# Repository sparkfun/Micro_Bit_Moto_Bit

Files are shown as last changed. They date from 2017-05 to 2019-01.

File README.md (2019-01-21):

SparkFun moto:bit
========================================

SparkFun moto:bit

[*SparkFun moto:bit (DEV-14213)*](https://www.sparkfun.com/products/14213)

The SparkFun moto:bit is a fully loaded “carrier” board for the micro:bit that, when combined with the micro:bit, provides you with a fully functional robotics platform. The moto:bit offers a simple, beginner-friendly robotics controller capable of operating a basic robotics chassis. Onboard each moto:bit are multiple I/O pins capable of hooking up servos, sensors and other circuits. At the flip of the switch you can get your micro:bit moving!

Repository Contents
-------------------

* **/Firmware** - Example code used in the micro:bot Kit Experiment Guide and Wireless Remote Control with micro:bit tutorials. While they are compiled HEX codes, you can modify the example code once they are imported into MakeCode editor.
* **/Hardware** - Eagle design files (.brd, .sch)
* **/Production** - Production panel files (.brd)

Documentation
--------------
* **[Library](https://github.com/sparkfun/pxt-moto-bit)** - PXT gamer:bit firmware
* **[micro:bot Kit Experiment Guide](https://learn.sparkfun.com/tutorials/microbot-kit-experiment-guide/)** - Experiment guide using the moto:bit carrier board.
* **[Wireless Remote Control with micro:bit](https://learn.sparkfun.com/tutorials/wireless-remote-control-with-microbit)** - Project guide using the micro:bot and micro:arcade kits. By utilizing the radio blocks, you can wirelessly control the micro:bot using the gamer:bit.

License Information
-------------------

This product is _**open source**_! 

Please review the LICENSE.md file for license information. 

If you have any questions or concerns on licensing, please contact techsupport@sparkfun.com.

Distributed as-is; no warranty is given.

- Your friends at SparkFun.

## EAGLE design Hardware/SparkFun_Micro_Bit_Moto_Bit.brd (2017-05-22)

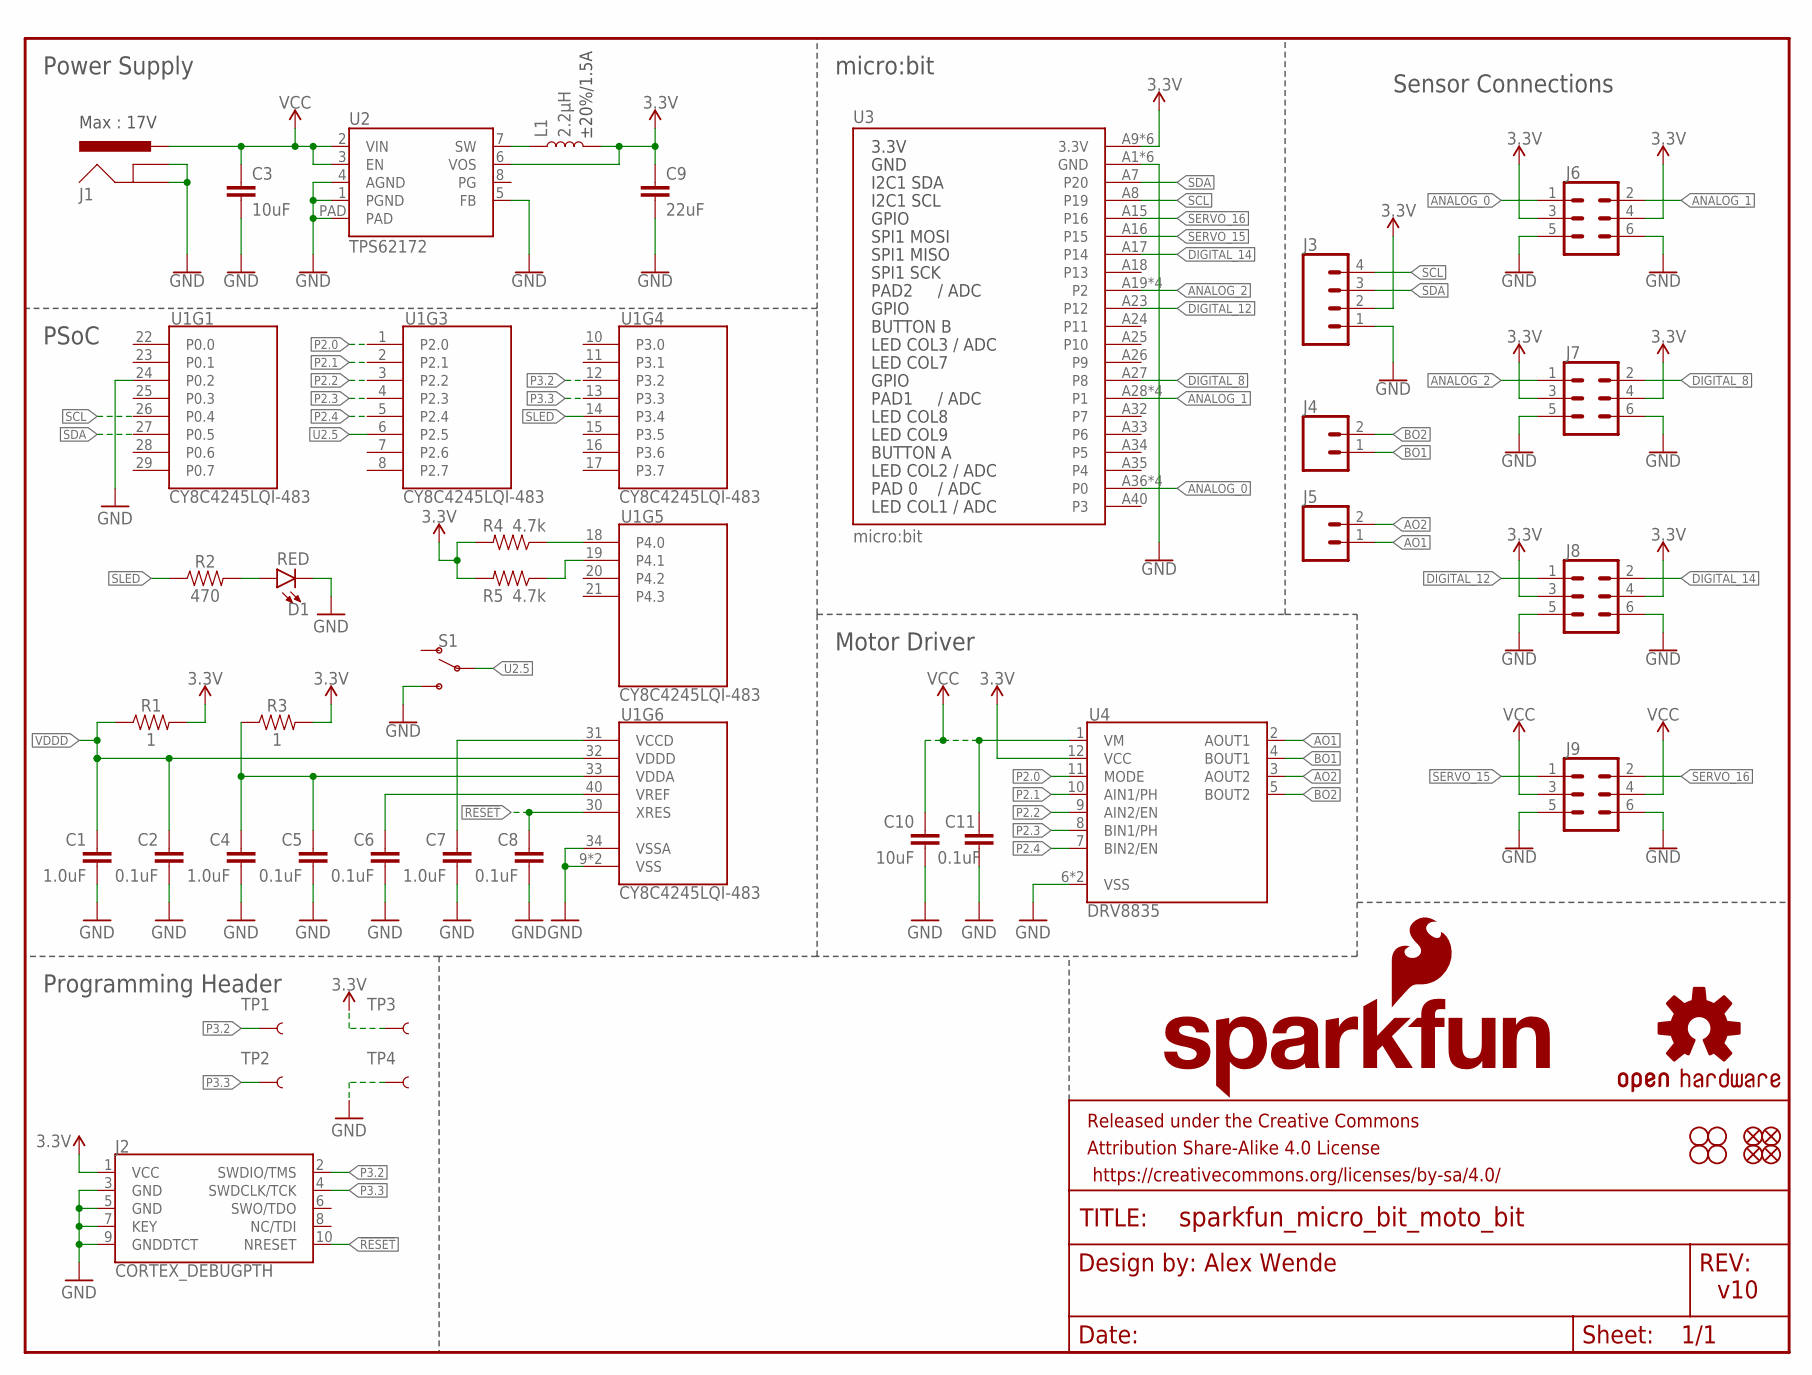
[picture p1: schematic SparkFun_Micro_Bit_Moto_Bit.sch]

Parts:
C1, C4, C7: 1.0uF; 0603
C2, C5, C6, C8, C11: 0.1uF; 0603
C3, C10: 10uF; 1210
C9: 22uF; 0805
D1: RED; LED-0603
FD1, FD2, FD3, FD4: FIDUCIALUFIDUCIAL; FIDUCIAL-MICRO
FRAME1: FRAME-LETTER; CREATIVE_COMMONS
H1, H2, H3, H4: STAND-OFF
J1: POWER_JACKPTH_LOCK; POWER_JACK_PTH_LOCK
J2: CORTEX_DEBUGPTH; 2X5-PTH-1.27MM
J3: CONN_04SMD_STRAIGHT_COMBO; 1X04_SMD_VERTICAL_COMBO
J4, J5: CONN_02PTH_RA_FEMALE; 1X02_RA_FEMALE
J6, J7, J8, J9: CONN_03X2SMT; 2X3_SMT_POSTS
L1: 2.2µH; INDUCTOR_2.2UH
LOGO1: SFE_LOGO_NAME_FLAME.3_INCH; SFE_LOGO_NAME_FLAME_.3
LOGO2: OSHW-LOGOL; OSHW-LOGO-L
R1, R3: 1; 0603
R2: 470; 0603
R4, R5: 4.7k; 0603
S1: SWITCH-SPDT-PTH-11.6X4.0MM; SWITCH_SPDT_PTH_11.6X4.0MM
TP1, TP2, TP3, TP4: TEST-POINT3; PAD.03X.03
U1: CY8C4245LQI-483; QFN-40
U2: TPS62172; WSON-8-PAD
U3: micro:bit; MICRO:BIT_RA_PTH
U4: DRV8835; WSON-12

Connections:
3.3V: C9.1, J2.1 (VCC), J3.2, J6.3, J6.4, J7.3, J7.4, J8.3, J8.4, L1.P$2 (2), R1.2, R3.2, R4.2, R5.2, TP3.P$1, U2.6 (VOS), U3.A9 (3.3V), U3.A10 (3.3V), U3.A11 (3.3V), U3.A12 (3.3V), U3.A13 (3.3V), U3.A14 (3.3V), U4.12 (VCC)
!RESET: C8.1, J2.10 (NRESET), U1.30 (XRES)
ANALOG_0: J6.1, U3.A36 (P0), U3.A37 (P0), U3.A38 (P0), U3.A39 (P0)
ANALOG_1: J6.2, U3.A28 (P1), U3.A29 (P1), U3.A30 (P1), U3.A31 (P1)
ANALOG_2: J7.1, U3.A19 (P2), U3.A20 (P2), U3.A21 (P2), U3.A22 (P2)
AO1: J5.1, U4.2 (AOUT1)
AO2: J5.2, U4.3 (AOUT2)
BO1: J4.1, U4.4 (BOUT1)
BO2: J4.2, U4.5 (BOUT2)
DIGITAL_8: J7.2, U3.A27 (P8)
DIGITAL_12: J8.1, U3.A23 (P12)
DIGITAL_14: J8.2, U3.A17 (P14)
GND: C1.2, C2.2, C3.2, C4.2, C5.2, C6.2, C7.2, C8.2, C9.2, C10.2, C11.2, D1.C, J1.GND, J1.GNDBREAK, J2.3 (GND), J2.5 (GND), J2.7 (KEY), J2.9 (GNDDTCT), J3.1, J6.5, J6.6, J7.5, J7.6, J8.5, J8.6, J9.5, J9.6, S1.3 (S), TP4.P$1, U1.9 (VSS), U1.24 (P0.2), U1.34 (VSSA), U1.EP (VSS), U2.1 (PGND), U2.4 (AGND), U2.5 (FB), U2.PAD, U3.A1 (GND), U3.A2 (GND), U3.A3 (GND), U3.A4 (GND), U3.A5 (GND), U3.A6 (GND), U4.6 (VSS), U4.PAD (VSS)
unnamed: C7.1, U1.31 (VCCD)
unnamed: C6.1, U1.40 (VREF)
unnamed: C4.1, C5.1, R3.1, U1.33 (VDDA)
unnamed: L1.P$1 (1), U2.7 (SW)
unnamed: R4.1, U1.18 (P4.0)
unnamed: R5.1, U1.19 (P4.1)
unnamed: D1.A, R2.2
P2.0: U1.1 (P2.0), U4.11 (MODE)
P2.1: U1.2 (P2.1), U4.10 (AIN1/PH)
P2.2: U1.3 (P2.2), U4.9 (AIN2/EN)
P2.3: U1.4 (P2.3), U4.8 (BIN1/PH)
P2.4: U1.5 (P2.4), U4.7 (BIN2/EN)
P3.2: J2.2 (SWDIO/TMS), TP1.P$1, U1.12 (P3.2)
P3.3: J2.4 (SWDCLK/TCK), TP2.P$1, U1.13 (P3.3)
SCL: J3.4, U1.26 (P0.4), U3.A8 (P19)
SDA: J3.3, U1.27 (P0.5), U3.A7 (P20)
SERVO_15: J9.1, U3.A16 (P15)
SERVO_16: J9.2, U3.A15 (P16)
SLED: R2.1, U1.14 (P3.4)
U2.5: S1.2, U1.6 (P2.5)
VCC: C3.1, C10.1, C11.1, J1.PWR, J9.3, J9.4, U2.2 (VIN), U2.3 (EN), U4.1 (VM)
VDDD: C1.1, C2.1, R1.1, U1.32 (VDDD)

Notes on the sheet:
±20%/1.5A
Power Supply
Motor Driver
Sensor Connections
micro:bit
Alex Wende
v10
PSoC
Programming Header
Max : 17V

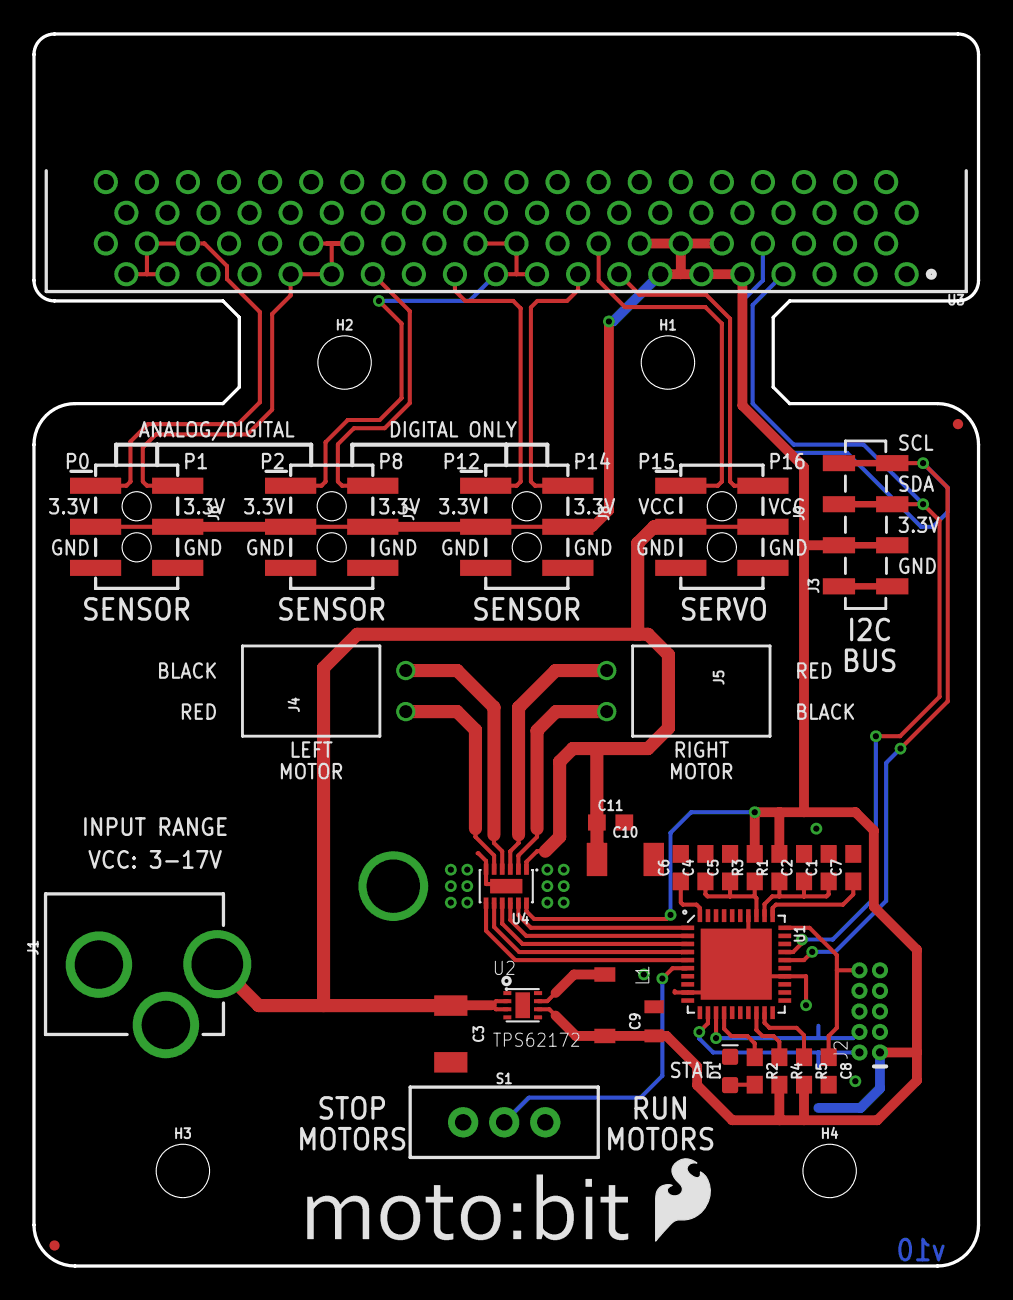
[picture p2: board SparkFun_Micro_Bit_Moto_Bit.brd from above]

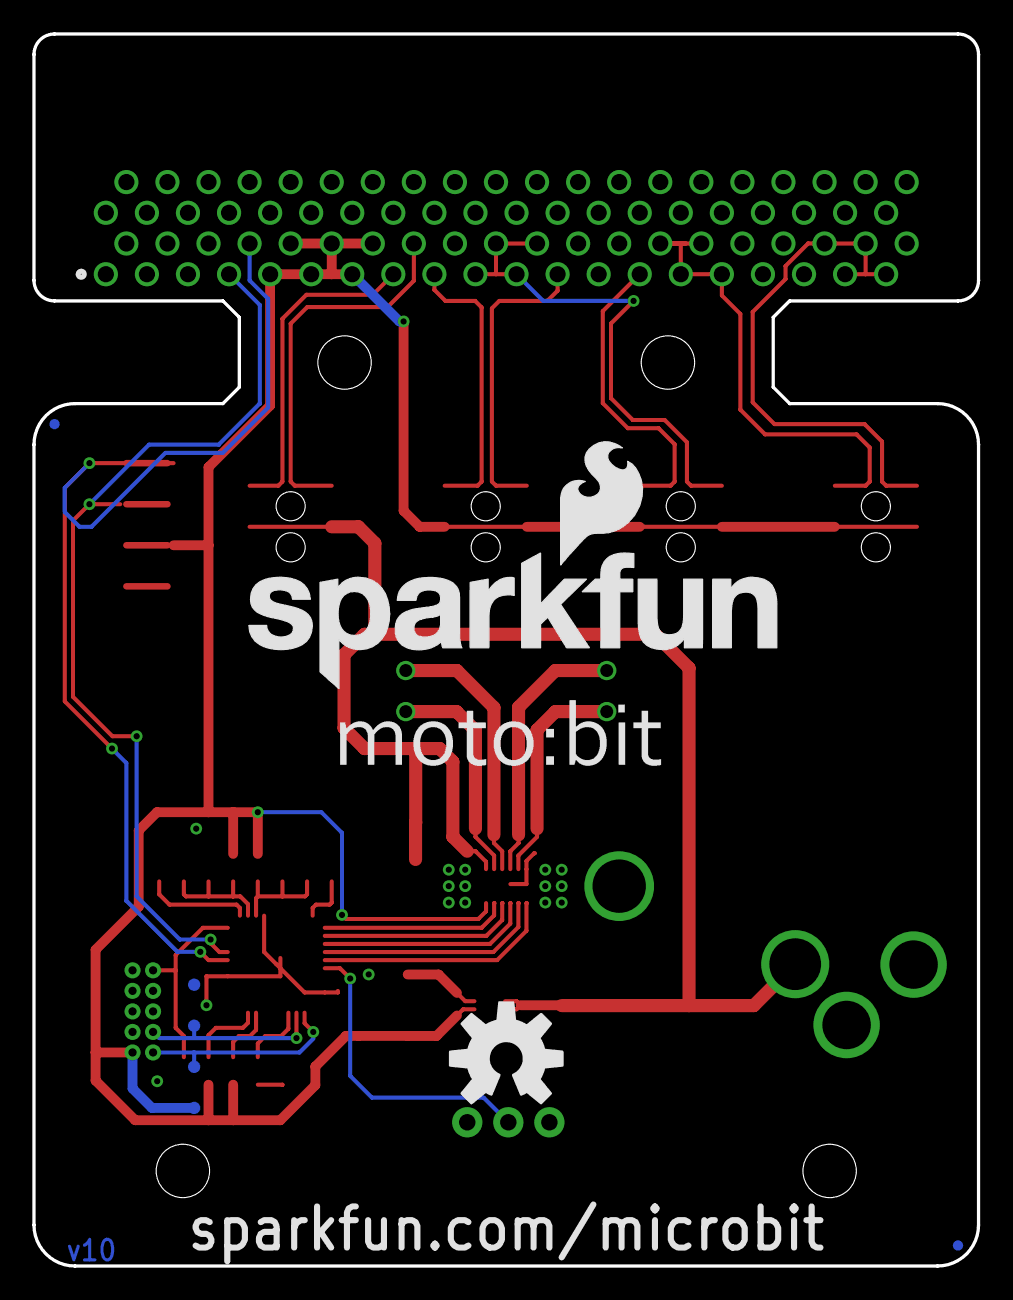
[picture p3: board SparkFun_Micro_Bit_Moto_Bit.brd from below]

Board: 2 copper layers, 58.4 x 76.2 mm, 51 parts (9 on the bottom side), 35 nets.

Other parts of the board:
U$1: PRODUCTION_INSTRUCTIONS
U$2: SFE_LOGO_FLAME_.2
U$3, U$4: LOGO-MOTOBIT

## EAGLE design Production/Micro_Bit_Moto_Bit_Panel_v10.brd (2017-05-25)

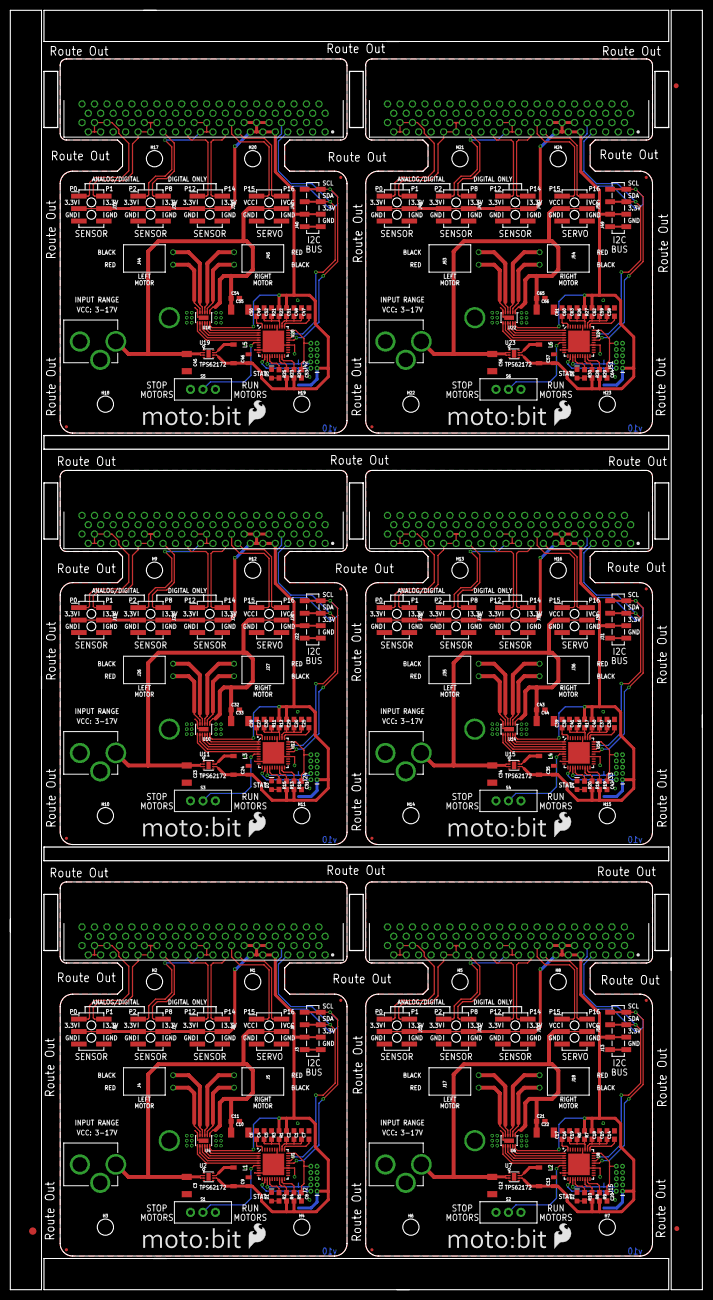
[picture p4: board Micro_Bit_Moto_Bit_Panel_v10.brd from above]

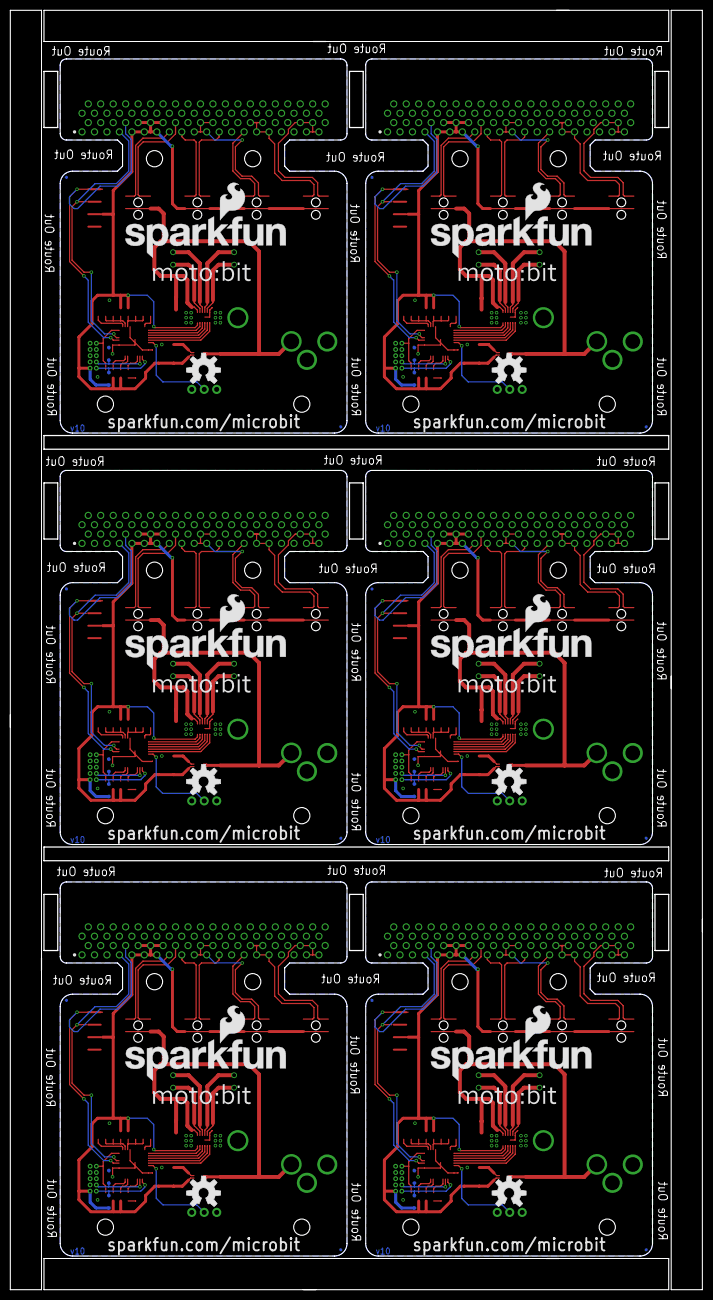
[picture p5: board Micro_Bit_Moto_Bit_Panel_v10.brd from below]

Board: 2 copper layers, 141.0 x 260.6 mm, 297 parts (54 on the bottom side), 210 nets.

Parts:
C1, C4, C7, C14, C15, C16, C25, C26, C27, C36, C37, C38, C47, C48, C49, C58, C59, C60: 1.0uF; 0603
C2, C5, C6, C8, C11, C17, C18, C19, C20, C21, C28, C29, C30, C31, C32, C39, C40, C41, C42, C43, C50, C51, C52, C53, C54, C61, C62, C63, C64, C65: 0.1uF; 0603
C3, C10, C12, C22, C23, C33, C34, C44, C45, C55, C56, C66: 10uF; 1210
C9, C13, C24, C35, C46, C57: 22uF; 0805
D1, D2, D3, D4, D5, D6: RED; LED-0603
E$1: FIDUCIAL-1.5X3
E$5, E$7: FIDUCIAL-1X2
FD1, FD2, FD3, FD4, FD5, FD6, FD7, FD8, FD9, FD10, FD11, FD12, FD13, FD14, FD15, FD16, FD17, FD18, FD19, FD20, FD21, FD22, FD23, FD24: FIDUCIALUFIDUCIAL; FIDUCIAL-MICRO
H1, H2, H3, H4, H5, H6, H7, H8, H9, H10, H11, H12, H13, H14, H15, H16, H17, H18, H19, H20, H21, H22, H23, H24: STAND-OFF
J1, J14, J23, J32, J41, J50: POWER_JACKPTH_LOCK; POWER_JACK_PTH_LOCK
J2, J15, J24, J33, J42, J51: CORTEX_DEBUGPTH; 2X5-PTH-1.27MM
J3, J13, J22, J31, J40, J49: 1X04_SMD_VERTICAL_COMBO
J4, J5, J17, J18, J26, J27, J35, J36, J44, J45, J53, J54: 1X02_RA_FEMALE
J6, J7, J8, J9, J10, J11, J12, J16, J19, J20, J21, J25, J28, J29, J30, J34, J37, J38, J39, J43, J46, J47, J48, J52: 2X3_SMT_POSTS
L1, L2, L3, L4, L5, L6: 2.2µH; INDUCTOR_2.2UH
LOGO1, LOGO3, LOGO5, LOGO7, LOGO9, LOGO11: SFE_LOGO_NAME_FLAME.3_INCH; SFE_LOGO_NAME_FLAME_.3
LOGO2, LOGO4, LOGO6, LOGO8, LOGO10, LOGO12: OSHW-LOGOL; OSHW-LOGO-L
R1, R3, R6, R7, R11, R12, R16, R17, R21, R22, R26, R27: 1; 0603
R2, R10, R15, R20, R25, R30: 470; 0603
R4, R5, R8, R9, R13, R14, R18, R19, R23, R24, R28, R29: 4.7k; 0603
S1, S2, S3, S4, S5, S6: SWITCH_SPDT_PTH_11.6X4.0MM
TP1, TP2, TP3, TP4, TP5, TP6, TP7, TP8, TP9, TP10, TP11, TP12, TP13, TP14, TP15, TP16, TP17, TP18, TP19, TP20, TP21, TP22, TP23, TP24: PAD.03X.03
U1, U8, U12, U16, U20, U24: CY8C4245LQI-483; QFN-40
U2, U7, U11, U15, U19, U23: TPS62172; WSON-8-PAD
U3, U5, U9, U13, U17, U21: micro:bit; MICRO:BIT_RA_PTH
U4, U6, U10, U14, U18, U22: DRV8835; WSON-12
U$2, U$5, U$8, U$11, U$14, U$17: SFE_LOGO_FLAME_.2
U$3, U$4, U$6, U$7, U$9, U$10, U$12, U$13, U$15, U$16, U$18, U$19: LOGO-MOTOBIT

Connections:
3.3V: C9.1, J2.1, J3.2, J6.3, J6.4, J7.3, J7.4, J8.3, J8.4, L1.P$2, R1.2, R3.2, R4.2, R5.2, TP3.P$1, U2.6, U3.A9, U3.A10, U3.A11, U3.A12, U3.A13, U3.A14, U4.12
3.3V1: C13.1, J10.3, J10.4, J11.3, J11.4, J12.3, J12.4, J13.2, J15.1, L2.P$2, R6.2, R7.2, R8.2, R9.2, TP7.P$1, U5.A9, U5.A10, U5.A11, U5.A12, U5.A13, U5.A14, U6.12, U7.6
3.3V2: C24.1, J19.3, J19.4, J20.3, J20.4, J21.3, J21.4, J22.2, J24.1, L3.P$2, R11.2, R12.2, R13.2, R14.2, TP11.P$1, U9.A9, U9.A10, U9.A11, U9.A12, U9.A13, U9.A14, U10.12, U11.6
3.3V3: C35.1, J28.3, J28.4, J29.3, J29.4, J30.3, J30.4, J31.2, J33.1, L4.P$2, R16.2, R17.2, R18.2, R19.2, TP15.P$1, U13.A9, U13.A10, U13.A11, U13.A12, U13.A13, U13.A14, U14.12, U15.6
3.3V4: C46.1, J37.3, J37.4, J38.3, J38.4, J39.3, J39.4, J40.2, J42.1, L5.P$2, R21.2, R22.2, R23.2, R24.2, TP19.P$1, U17.A9, U17.A10, U17.A11, U17.A12, U17.A13, U17.A14, U18.12, U19.6
3.3V5: C57.1, J46.3, J46.4, J47.3, J47.4, J48.3, J48.4, J49.2, J51.1, L6.P$2, R26.2, R27.2, R28.2, R29.2, TP23.P$1, U21.A9, U21.A10, U21.A11, U21.A12, U21.A13, U21.A14, U22.12, U23.6
!RESET: C8.1, J2.10, U1.30
!RESET1: C20.1, J15.10, U8.30
!RESET2: C31.1, J24.10, U12.30
!RESET3: C42.1, J33.10, U16.30
!RESET4: C53.1, J42.10, U20.30
!RESET5: C64.1, J51.10, U24.30
ANALOG_0: J6.1, U3.A36, U3.A37, U3.A38, U3.A39
ANALOG_1: J6.2, U3.A28, U3.A29, U3.A30, U3.A31
ANALOG_2: J7.1, U3.A19, U3.A20, U3.A21, U3.A22
ANALOG_3: J11.1, U5.A19, U5.A20, U5.A21, U5.A22
ANALOG_4: J10.2, U5.A28, U5.A29, U5.A30, U5.A31
ANALOG_5: J10.1, U5.A36, U5.A37, U5.A38, U5.A39
ANALOG_6: J20.1, U9.A19, U9.A20, U9.A21, U9.A22
ANALOG_7: J19.2, U9.A28, U9.A29, U9.A30, U9.A31
ANALOG_8: J19.1, U9.A36, U9.A37, U9.A38, U9.A39
ANALOG_9: J29.1, U13.A19, U13.A20, U13.A21, U13.A22
ANALOG_10: J28.2, U13.A28, U13.A29, U13.A30, U13.A31
ANALOG_11: J28.1, U13.A36, U13.A37, U13.A38, U13.A39
ANALOG_12: J38.1, U17.A19, U17.A20, U17.A21, U17.A22
ANALOG_13: J37.2, U17.A28, U17.A29, U17.A30, U17.A31
ANALOG_14: J37.1, U17.A36, U17.A37, U17.A38, U17.A39
ANALOG_15: J47.1, U21.A19, U21.A20, U21.A21, U21.A22
ANALOG_16: J46.2, U21.A28, U21.A29, U21.A30, U21.A31
ANALOG_17: J46.1, U21.A36, U21.A37, U21.A38, U21.A39
AO1: J5.1, U4.2
AO2: J5.2, U4.3
AO3: J18.1, U6.2
AO4: J18.2, U6.3
AO5: J27.1, U10.2
AO6: J27.2, U10.3
AO7: J36.1, U14.2
AO8: J36.2, U14.3
AO9: J45.1, U18.2
AO10: J45.2, U18.3
AO11: J54.1, U22.2
AO12: J54.2, U22.3
BO1: J4.1, U4.4
BO2: J4.2, U4.5
BO3: J17.1, U6.4
BO4: J17.2, U6.5
BO5: J26.1, U10.4
BO6: J26.2, U10.5
BO7: J35.1, U14.4
BO8: J35.2, U14.5
BO9: J44.1, U18.4
BO10: J44.2, U18.5
BO11: J53.1, U22.4
BO12: J53.2, U22.5
DIGITAL_1: J11.2, U5.A27
DIGITAL_2: J12.1, U5.A23
DIGITAL_3: J12.2, U5.A17
DIGITAL_4: J20.2, U9.A27
DIGITAL_5: J21.1, U9.A23
DIGITAL_6: J21.2, U9.A17
DIGITAL_7: J29.2, U13.A27
DIGITAL_8: J7.2, U3.A27
DIGITAL_9: J30.1, U13.A23
DIGITAL_10: J30.2, U13.A17
DIGITAL_11: J38.2, U17.A27
DIGITAL_12: J8.1, U3.A23
DIGITAL_13: J39.1, U17.A23
DIGITAL_14: J8.2, U3.A17
DIGITAL_15: J39.2, U17.A17
DIGITAL_16: J47.2, U21.A27
DIGITAL_17: J48.1, U21.A23
DIGITAL_18: J48.2, U21.A17
GND: C1.2, C2.2, C3.2, C4.2, C5.2, C6.2, C7.2, C8.2, C9.2, C10.2, C11.2, D1.C, J1.GND, J1.GNDBREAK, J2.3, J2.5, J2.7, J2.9, J3.1, J6.5, J6.6, J7.5, J7.6, J8.5, J8.6, J9.5, J9.6, S1.3, TP4.P$1, U1.9, U1.24, U1.34, U1.EP, U2.1, U2.4, U2.5, U2.PAD, U3.A1, U3.A2, U3.A3, U3.A4, U3.A5, U3.A6, U4.6, U4.PAD
GND1: C12.2, C13.2, C14.2, C15.2, C16.2, C17.2, C18.2, C19.2, C20.2, C21.2, C22.2, D2.C, J10.5, J10.6, J11.5, J11.6, J12.5, J12.6, J13.1, J14.GND, J14.GNDBREAK, J15.3, J15.5, J15.7, J15.9, J16.5, J16.6, S2.3, TP8.P$1, U5.A1, U5.A2, U5.A3, U5.A4, U5.A5, U5.A6, U6.6, U6.PAD, U7.1, U7.4, U7.5, U7.PAD, U8.9, U8.24, U8.34, U8.EP
GND2: C23.2, C24.2, C25.2, C26.2, C27.2, C28.2, C29.2, C30.2, C31.2, C32.2, C33.2, D3.C, J19.5, J19.6, J20.5, J20.6, J21.5, J21.6, J22.1, J23.GND, J23.GNDBREAK, J24.3, J24.5, J24.7, J24.9, J25.5, J25.6, S3.3, TP12.P$1, U9.A1, U9.A2, U9.A3, U9.A4, U9.A5, U9.A6, U10.6, U10.PAD, U11.1, U11.4, U11.5, U11.PAD, U12.9, U12.24, U12.34, U12.EP
GND3: C34.2, C35.2, C36.2, C37.2, C38.2, C39.2, C40.2, C41.2, C42.2, C43.2, C44.2, D4.C, J28.5, J28.6, J29.5, J29.6, J30.5, J30.6, J31.1, J32.GND, J32.GNDBREAK, J33.3, J33.5, J33.7, J33.9, J34.5, J34.6, S4.3, TP16.P$1, U13.A1, U13.A2, U13.A3, U13.A4, U13.A5, U13.A6, U14.6, U14.PAD, U15.1, U15.4, U15.5, U15.PAD, U16.9, U16.24, U16.34, U16.EP
GND4: C45.2, C46.2, C47.2, C48.2, C49.2, C50.2, C51.2, C52.2, C53.2, C54.2, C55.2, D5.C, J37.5, J37.6, J38.5, J38.6, J39.5, J39.6, J40.1, J41.GND, J41.GNDBREAK, J42.3, J42.5, J42.7, J42.9, J43.5, J43.6, S5.3, TP20.P$1, U17.A1, U17.A2, U17.A3, U17.A4, U17.A5, U17.A6, U18.6, U18.PAD, U19.1, U19.4, U19.5, U19.PAD, U20.9, U20.24, U20.34, U20.EP
GND5: C56.2, C57.2, C58.2, C59.2, C60.2, C61.2, C62.2, C63.2, C64.2, C65.2, C66.2, D6.C, J46.5, J46.6, J47.5, J47.6, J48.5, J48.6, J49.1, J50.GND, J50.GNDBREAK, J51.3, J51.5, J51.7, J51.9, J52.5, J52.6, S6.3, TP24.P$1, U21.A1, U21.A2, U21.A3, U21.A4, U21.A5, U21.A6, U22.6, U22.PAD, U23.1, U23.4, U23.5, U23.PAD, U24.9, U24.24, U24.34, U24.EP
unnamed: C7.1, U1.31
unnamed: C6.1, U1.40
unnamed: C4.1, C5.1, R3.1, U1.33
unnamed: L1.P$1, U2.7
unnamed: L2.P$1, U7.7
unnamed: R4.1, U1.18
unnamed: R5.1, U1.19
unnamed: D1.A, R2.2
unnamed: C14.1, U8.31
unnamed: C16.1, C19.1, R6.1, U8.33
unnamed: C17.1, U8.40
unnamed: R8.1, U8.18
unnamed: R9.1, U8.19
unnamed: D2.A, R10.2
unnamed: L3.P$1, U11.7
unnamed: C25.1, U12.31
unnamed: C27.1, C30.1, R11.1, U12.33
unnamed: C28.1, U12.40
unnamed: R13.1, U12.18
unnamed: R14.1, U12.19
unnamed: D3.A, R15.2
unnamed: L4.P$1, U15.7
unnamed: C36.1, U16.31
unnamed: C38.1, C41.1, R16.1, U16.33
unnamed: C39.1, U16.40
unnamed: R18.1, U16.18
unnamed: R19.1, U16.19
unnamed: D4.A, R20.2
unnamed: L5.P$1, U19.7
unnamed: C47.1, U20.31
unnamed: C49.1, C52.1, R21.1, U20.33
unnamed: C50.1, U20.40
unnamed: R23.1, U20.18
unnamed: R24.1, U20.19
unnamed: D5.A, R25.2
unnamed: L6.P$1, U23.7
unnamed: C58.1, U24.31
unnamed: C60.1, C63.1, R26.1, U24.33
unnamed: C61.1, U24.40
unnamed: R28.1, U24.18
unnamed: R29.1, U24.19
unnamed: D6.A, R30.2
P2.0: U1.1, U4.11
P2.1: U1.2, U4.10
P2.2: U1.3, U4.9
P2.3: U1.4, U4.8
P2.4: U1.5, U4.7
P2.5: U6.10, U8.2
P2.6: U6.9, U8.3
P2.7: U6.8, U8.4
P2.8: U6.7, U8.5
P2.9: U6.11, U8.1
P2.10: U10.10, U12.2
P2.11: U10.9, U12.3
P2.12: U10.8, U12.4
P2.13: U10.7, U12.5
P2.14: U10.11, U12.1
P2.15: U14.10, U16.2
P2.16: U14.9, U16.3
P2.17: U14.8, U16.4
P2.18: U14.7, U16.5
P2.19: U14.11, U16.1
P2.20: U18.10, U20.2
P2.21: U18.9, U20.3
P2.22: U18.8, U20.4
P2.23: U18.7, U20.5
P2.24: U18.11, U20.1
P2.25: U22.10, U24.2
P2.26: U22.9, U24.3
P2.27: U22.8, U24.4
P2.28: U22.7, U24.5
P2.29: U22.11, U24.1
P3.1: J15.2, TP5.P$1, U8.12
P3.2: J2.2, TP1.P$1, U1.12
P3.3: J2.4, TP2.P$1, U1.13
P3.4: J15.4, TP6.P$1, U8.13
P3.5: J24.2, TP9.P$1, U12.12
P3.6: J24.4, TP10.P$1, U12.13
P3.7: J33.2, TP13.P$1, U16.12
P3.8: J33.4, TP14.P$1, U16.13
P3.9: J42.2, TP17.P$1, U20.12
P3.10: J42.4, TP18.P$1, U20.13
P3.11: J51.2, TP21.P$1, U24.12
P3.12: J51.4, TP22.P$1, U24.13
SCL: J3.4, U1.26, U3.A8
SCL1: J13.4, U5.A8, U8.26
SCL2: J22.4, U9.A8, U12.26
SCL3: J31.4, U13.A8, U16.26
SCL4: J40.4, U17.A8, U20.26
SCL5: J49.4, U21.A8, U24.26
SDA: J3.3, U1.27, U3.A7
SDA1: J13.3, U5.A7, U8.27
SDA2: J22.3, U9.A7, U12.27
SDA3: J31.3, U13.A7, U16.27
SDA4: J40.3, U17.A7, U20.27
SDA5: J49.3, U21.A7, U24.27
SERVO_1: J16.2, U5.A15
SERVO_2: J16.1, U5.A16
SERVO_3: J25.2, U9.A15
SERVO_4: J25.1, U9.A16
SERVO_5: J34.2, U13.A15
SERVO_6: J34.1, U13.A16
SERVO_7: J43.2, U17.A15
SERVO_8: J43.1, U17.A16
SERVO_9: J52.2, U21.A15
SERVO_10: J52.1, U21.A16
SERVO_15: J9.1, U3.A16
SERVO_16: J9.2, U3.A15
SLED: R2.1, U1.14
SLED1: R10.1, U8.14
SLED2: R15.1, U12.14
SLED3: R20.1, U16.14
SLED4: R25.1, U20.14
SLED5: R30.1, U24.14
U2.1: S2.2, U8.6
U2.2: S3.2, U12.6
U2.3: S4.2, U16.6
U2.4: S5.2, U20.6
U2.5: S1.2, U1.6
U2.6: S6.2, U24.6
VCC: C3.1, C10.1, C11.1, J1.PWR, J9.3, J9.4, U2.2, U2.3, U4.1
VCC1: C12.1, C21.1, C22.1, J14.PWR, J16.3, J16.4, U6.1, U7.2, U7.3
VCC2: C23.1, C32.1, C33.1, J23.PWR, J25.3, J25.4, U10.1, U11.2, U11.3
VCC3: C34.1, C43.1, C44.1, J32.PWR, J34.3, J34.4, U14.1, U15.2, U15.3
VCC4: C45.1, C54.1, C55.1, J41.PWR, J43.3, J43.4, U18.1, U19.2, U19.3
VCC5: C56.1, C65.1, C66.1, J50.PWR, J52.3, J52.4, U22.1, U23.2, U23.3
VDDD: C1.1, C2.1, R1.1, U1.32
VDDD1: C15.1, C18.1, R7.1, U8.32
VDDD2: C26.1, C29.1, R12.1, U12.32
VDDD3: C37.1, C40.1, R17.1, U16.32
VDDD4: C48.1, C51.1, R22.1, U20.32
VDDD5: C59.1, C62.1, R27.1, U24.32

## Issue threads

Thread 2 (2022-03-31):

Is there any documentation on the I2C bus protocol?

nlbutts, 2022-03-31:
I bought a bunch of these MotoBit boards for the Boy Scouts. I want to use the board with a Jetson to drive DC and servo motors. Can I do that through the MotoBIT via I2C?

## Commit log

2017-03-30 v01 changes
    -Added 4.7k pullups to PSoC pins 4.0 and 4.1
    - Added status LED
    [motobit.brd, motobit.sch]
2017-03-30 Changed name from motobit to follow naming conventions
    [SparkFun_Micro_Bit_Moto_Bit.brd, SparkFun_Micro_Bit_Moto_Bit.sch, motobit.brd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]
2017-03-31 Design Review Changes
    - Added staking vias to barrel connector and motor connector
    - Added two servo connectors
    - Moved vias that were exposed for motor driver heatsink
    - Added selective solder path
    - Added mounting holes
    - Rounded corners to match micro:bit
    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
    [SparkFun_Micro_Bit_Moto_Bit.brd, SparkFun_Micro_Bit_Moto_Bit.sch]
2017-04-03 QC Fixes
    - Removed excess copper around PSoC center pad
    - Added names and values to buck converter and inductor
    - Added note about solder mask color finish
    [SparkFun_Micro_Bit_Moto_Bit.brd, SparkFun_Micro_Bit_Moto_Bit.sch]
2017-04-18 Updated Changes
    Made a bunch of changes based on suggestions from education
    [SparkFun_Micro_Bit_Moto_Bit.brd, SparkFun_Micro_Bit_Moto_Bit.sch]
2017-04-19 Updated Measures Layer
    [SparkFun_Micro_Bit_Moto_Bit.brd, SparkFun_Micro_Bit_Moto_Bit.sch]
2017-04-20 Design review changes
    [SparkFun_Micro_Bit_Moto_Bit.brd, SparkFun_Micro_Bit_Moto_Bit.sch]
2017-04-20 Fixed part number for 2 pin female header
    [SparkFun_Micro_Bit_Moto_Bit.brd, SparkFun_Micro_Bit_Moto_Bit.sch]
2017-04-21 Rounded Corners
    [SparkFun_Micro_Bit_Moto_Bit.brd]
2017-05-18 V10 Changes
    - Replaced 2x3 female headers to male
    - Changed net label on heatsink mounting hole to GND
    - Increased distance between exposed pad and motor connectors
    [SparkFun_Micro_Bit_Moto_Bit.brd, SparkFun_Micro_Bit_Moto_Bit.sch]
2017-05-22 Touched up traces
    A few traces had 90deg bends, replaced with 45deg bends
    [SparkFun_Micro_Bit_Moto_Bit.brd]
2017-05-25 created panel v10
    [Micro_Bit_Moto_Bit_Panel_v10.brd]
2019-01-21 Add Wireless Remote Control with micro:bit examples
2020-01-22 Fix Bugs in Examples Using Line Following Sensors
    - Update experiment 2 and 3 with improved line following examples for with option to debug via MakeCode console. Previous examples did not actually read a dark surface correctly...
    - Add some animated arrows for the user to see what button to press when the micro:bit initializes
    - Include notes for each condition statement
    - Broke up experiment 3 into two parts for users to easily digest.
    - Update battle bot example so it does not randomly "attack" based on line following readings on "collision." That's not how line following sensors work...

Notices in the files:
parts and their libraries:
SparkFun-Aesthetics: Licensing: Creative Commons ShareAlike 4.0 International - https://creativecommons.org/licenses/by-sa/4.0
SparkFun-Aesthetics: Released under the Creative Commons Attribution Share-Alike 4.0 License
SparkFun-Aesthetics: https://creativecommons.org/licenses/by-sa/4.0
